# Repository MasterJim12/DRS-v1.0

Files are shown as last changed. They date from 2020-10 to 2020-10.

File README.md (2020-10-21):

# DRS-v1.0
# Aero Code
  The main goal of the code is to provide functionality while keeping it readable for future team members that may not have a coding background.

# Board Design
  The goal of this board is to connect external servos and limit switches to the circuit board. It is also meant to handle power distribution between the components.

# Version 1.0 Issues
  With testing we found that pressing the button to activate the DRS system has bounce. This results in a less than ideal flap of the wings until the signal smooths out. 
  (A solution might be to add interupts to the code).
  The servos make noise and get hot after some time even if they aren't changin position. (This might be because of rubbing of wing elements which may be causing extra strain on the servos / I may need to design a BEC for power delivery to the servos)

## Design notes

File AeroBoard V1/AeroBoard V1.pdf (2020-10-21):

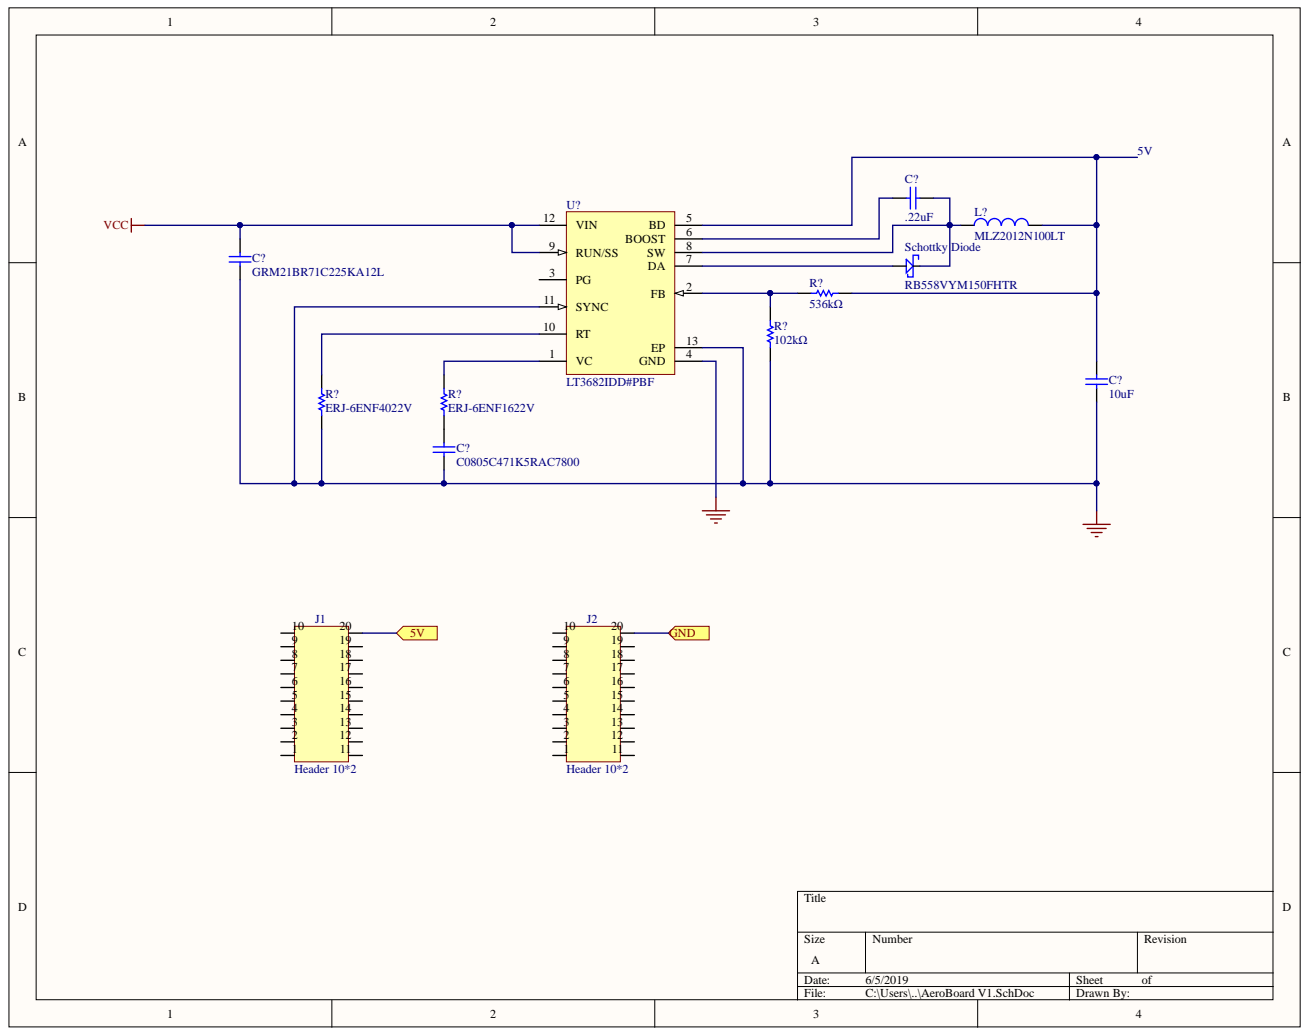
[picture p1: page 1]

R? ERJ-6ENF4022V | R? ERJ-6ENF1622V | LT3682IDD#PBF

# Board Stack Report

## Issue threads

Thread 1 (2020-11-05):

Servo Noise and Heat

MasterJim12, 2020-11-05:
Servos are making noise even when they are not in motion.
These are digital servos, which do produce some of these symptoms. The refresh rate might be too low. Check mechanical linkages to the car and sand out any parts that are rubbing.

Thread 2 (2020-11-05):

Bouncing Signals

MasterJim12, 2020-11-05:
Wings sometimes flap an extra time due to bounce from the button press. Implementing interrupts should help with this issue.

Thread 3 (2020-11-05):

Board to Wire Termination (AeroBoard)

MasterJim12, 2020-11-05:
We need to find some new connectors to connect the wires to the board. They need to be surface mount (Through hole has had an issue in the past where the carbon fiber from the wings short out the pins of the microcontroller. Maybe take a look at amphenol or deutsch connectors. Deutsch preferably since it is already used with the rest of the wiring harness. This should be 2 separate connectors, one for the limit switch's, the other should handle power and button input from the steering wheel.

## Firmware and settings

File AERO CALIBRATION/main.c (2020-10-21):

#include <stdint.h>
#include <stdbool.h>
#include "inc/hw_memmap.h"
#include "inc/hw_types.h"
#include "driverlib/sysctl.h"
#include "driverlib/gpio.h"
#include "driverlib/debug.h"
#include "driverlib/pwm.h"
#include "driverlib/pin_map.h"
#include "inc/hw_gpio.h"
#include "driverlib/rom.h"


#define PWM_FREQUENCY 300 // I am going to be using 300Hz because the website says that 333hz is the max refresh

// Need a function that changes the PWM s

int main(void)
{


    /*First when the system is turned on. I want the servo to move up first across a wide range of PWM Values. Once Switch it hit, record PWM Upper and stop.
    * Then I would like it to move downwards fully until it hits a switch, then record the value as PWMLower
    * If the switch is not hit at during the upper or lower bounds, and the pwm is maxed out. The max value will become the new upper and/or lower bound.
    * The upper and lower bound is the n divided by two, to produce the middle bound.
    */


        volatile uint32_t maxPWM = 0; // This variable is made to hold the MAX PWM value when it is found.
        volatile uint32_t minPWM = 0;// This variable is made to hold the minimum PWM value when it is found.

        /* Our servo has a frequency of 300Hz. The period based on this is .003333 Seconds. Or .3333mS
         * Dividing this by 1000 gives a resolution of .000003333S or 3.333uS
         * The median for most servos is at 1.5ms
         * So .000003333 * 450.045 gives us the median of 1.5ms
         */
       volatile uint32_t ui8Adjust = 450;

        ROM_SysCtlClockSet(SYSCTL_SYSDIV_5|SYSCTL_USE_PLL|SYSCTL_OSC_MAIN|SYSCTL_XTAL_16MHZ);//This runs the CPU at 40Mhz

        ROM_SysCtlPWMClockSet(SYSCTL_PWMDIV_64); // THE PWM is clocked through a divider that has a range from 2 to 64. This runs the PWM clock at 625kHz.

        ROM_SysCtlPeripheralEnable(SYSCTL_PERIPH_PWM1); // This enables the PWM Generator 1 Which controls PWM on Pins on Port D
        ROM_SysCtlPeripheralEnable(SYSCTL_PERIPH_GPIOD);// This enables pins on PortD, we need this for the pin that will output the PWM
        ROM_SysCtlPeripheralEnable(SYSCTL_PERIPH_GPIOF);// This enables pint on PortF, we need this for the pin that will take input from the buttons.

        ROM_GPIOPinTypePWM(GPIO_PORTD_BASE, GPIO_PIN_0); // This sets our pin to to PWM mode
        ROM_GPIOPinConfigure(GPIO_PD0_M1PWM0); // This configures PWM Generator 0 to handle the signal for our pin

        HWREG(GPIO_PORTF_BASE + GPIO_O_LOCK) = GPIO_LOCK_KEY;
        HWREG(GPIO_PORTF_BASE + GPIO_O_CR) |= 0x01;
        HWREG(GPIO_PORTF_BASE + GPIO_O_LOCK) = 0; //The previous lines unlock the GPIO commit Control register
        ROM_GPIODirModeSet(GPIO_PORTF_BASE, GPIO_PIN_4| GPIO_PIN_0, GPIO_DIR_MODE_IN); // This sets the PF0 and PF4 as inputs
        ROM_GPIOPadConfigSet(GPIO_PORTF_BASE, GPIO_PIN_4| GPIO_PIN_0, GPIO_STRENGTH_2MA, GPIO_PIN_TYPE_STD_WPU); // This configures the pull up resistors for PF0 and PF4 we need this to tell when the limit switches are pressed.
        ROM_GPIOPadConfigSet(GPIO_PORTD_BASE, GPIO_PIN_2, GPIO_STRENGTH_2MA, GPIO_PIN_TYPE_STD_WPU); // This configures the pull up resistors for PD2 so that we can read when the DRS button is pushed.

        volatile uint32_t ui32PWMClock = SysCtlClockGet() / 64;
        volatile uint32_t ui32Load = (ui32PWMClock / PWM_FREQUENCY ) -1;
        PWMGenConfigure(PWM1_BASE, PWM_GEN_0, PWM_GEN_MODE_DOWN);
        PWMGenPeriodSet (PWM1_BASE, PWM_GEN_0, ui32Load);

        ROM_PWMPulseWidthSet (PWM1_BASE, PWM_OUT_0, ui8Adjust * ui32Load / 1000); //This sets the min resolution of the servo.
        ROM_PWMOutputState(PWM1_BASE, PWM_OUT_0_BIT, true);// This sets the PWM generator to output its signal
        ROM_PWMGenEnable(PWM1_BASE, PWM_GEN_0); // This enables the PWM Generator to run


        // This section actually controls the initial startup sequence.
        // This code needs to be reworked in order to accommodate for the bounce of the switch or button.
            while ( minPWM == 0){
                    if (ROM_GPIOPinRead(GPIO_PORTF_BASE,GPIO_PIN_0) == 0x00 ){
                        minPWM = ui8Adjust - 5 ;
                    }
                    else ui8Adjust++;
                    if (ui8Adjust > 600 )
                    {
                        ui8Adjust = 600;
                        minPWM = ui8Adjust;
                    }
                    ROM_PWMPulseWidthSet(PWM1_BASE, PWM_OUT_0, ui8Adjust * ui32Load / 1000);
                    ROM_SysCtlDelay(100000);
                }

            while ( maxPWM == 0){
                           if (ROM_GPIOPinRead(GPIO_PORTF_BASE,GPIO_PIN_4) == 0x00 ){
                               maxPWM = ui8Adjust + 5 ;
                           }
                           else ui8Adjust--;
                           if (ui8Adjust < 300 )
                           {
                               ui8Adjust = 300;
                               maxPWM = ui8Adjust;
                           }
                           ROM_PWMPulseWidthSet(PWM1_BASE, PWM_OUT_0, ui8Adjust * ui32Load / 1000);
                           ROM_SysCtlDelay(100000);
                       }

            volatile uint32_t Done = 0; // This variable is used to create an infinite while loop
            while ( Done == 0){

                // This first part of the while loop searches to see if the DRS button, which should be connected to pin PD2 is being pressed down.
                // If it is the wings will open.
                if (ROM_GPIOPinRead(GPIO_PORTD_BASE,GPIO_PIN_2) != 0x00 ){
                    ROM_PWMPulseWidthSet(PWM1_BASE, PWM_OUT_0, maxPWM * ui32Load / 1000);
                }
                // This second part scans to see if the DRS button is not being pressed down.
                // If it is not then the wings will close.
                else ROM_PWMPulseWidthSet(PWM1_BASE, PWM_OUT_0, minPWM * ui32Load / 1000);
                //ROM_SysCtlDelay(10);
            }

}
